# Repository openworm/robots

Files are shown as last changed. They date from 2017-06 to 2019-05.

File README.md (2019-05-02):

# robots
C. elegans robots.

The goal of this project is twofold:
1. To build a robot that simulates the neuromuscular function of a C. elegans nematode worm.
2. To specify a kit of parts and instructions that will allow a student to also build the robot.

The robot is controlled by a Raspberry Pi/ESP32 processor that contains a recorded simulation of the worm's
neuromuscular system (see references). The robot's body is a sequence of segments that mutually exert simulated muscle
contractions impemented by servos.

Folders:
1. WormHost: PC code to communicate with the onboard Raspberry Pi.
2. WormRPi: Raspberry Pi onboard code.
3. WormESP32: ESP32 onboard code.
4. WormSim: C. elegans neuromuscular simulator.
5. assembly: parts list, 3D printing .stl shape files, and assembly instructions.
6. docs: robot description.

References:
Boyle, Berri and Cohen, "Gait modulation in C. elegans: an integrated neuromechanical model", Front. Comput. Neurosci., 2012.
Eduardo J. Izquierdo and Randall D. Beer, "An Integrated Neuromechanical Model of Steering in C. elegans", ECAL15

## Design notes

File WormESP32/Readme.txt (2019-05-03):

C elegans worm robot with ESP32.
A distance sensor simulates food foraging by locating and moving toward the nearest object.

Power up the ESP32 and connect to its network: Robot_Worm
ESP32 IP address should be 192.169.4.1

Transfer python and segment_angles.txt to ESP32 using ftp.

FTP:
For linux:
In ftp connection, issue "passive" command to avoid attempt to open a server-to-client data connection.
This connection will be refused.
Cygwin:
Get ftp by installing inetutils package (also gets telnet).
FileZilla instructions:
https://github.com/loboris/MicroPython_ESP32_psRAM_LoBo/wiki/ftpserver

Login with telnet: 
telnet 192.168.4.1
login=micro, password=python

Run scripts:
1. To straighten robot:
exec(open("servo_reset.py").read())
2. To test servos:
exec(open("servo_test.py").read())
3. Run no food sensor:
exec(open("worm_run_segment_angles.py").read())
4. Run with laser distance food sensor:
exec(open("worm_run_segment_angles_laser.py").read())
5. Run with ultrasonic distance food sensor:
exec(open("worm_run_segment_angles_sonic.py").read())

The maximim number of steps can be limited by creating a file named "max_steps.txt" containing the value.

Note: power cycle board if you encounter python errors after repeated runs.

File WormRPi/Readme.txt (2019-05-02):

C elegans worm robot Raspberry Pi Zero W code.

Download Raspbian to SD boot card.

To enable wireless, create wpa_supplicant.conf in boot directory with this content:
country=<country code, e.g. US>
ctrl_interface=DIR=/var/run/wpa_supplicant GROUP=netdev
update_config=1

network={
    ssid="<network name>"
    psk="<network password>"
}

To enable ssh, create file named "ssh" in boot directory.

To find RPi IP: nmap -sn 192.168.1.0/24

Enable I2C:
https://www.abelectronics.co.uk/kb/article/1/i2c--smbus-and-raspbian-linux

Login with ssh:
ssh <RPi IP>
login=pi, password=raspberry

Setup:
1. Create $HOME/robot directory on RPi:
mkdir $HOME/robot
2. Copy python and segment_angles.txt files to $HOME/robot.

Run scripts: servo_reset.py (straighten robot), worm_run.py, worm_run_angles.py, worm_run_segment_angles.py

Ultrasonic distance sensor:

Parallax Ping Ultrasonic distance sensor:
https://www.parallax.com/sites/default/files/downloads/28015-PING-Sensor-Product-Guide-v2.0.pdf
See: sonar.py

Deprecated audio sensor:
 
Audio microphone installation instructions:
https://learn.adafruit.com/adafruit-i2s-mems-microphone-breakout/
https://pinout.xyz/pinout/i2c#
See: food_listener.py

To set audio volume sensitivity:
Copy asoundrc.txt to $HOME/.asoundrc on the robot.
Run arecord first to "prime the pump"
Then either:
  alsamixer
    F6 to select snd_rpi_simple_card
    F4 to set volume
or
  amixer -M set Capture 50%
Finally to make sensitivity persistent:
  sudo alsactl store 1

To enable http communications with host:
1. Copy json files to $HOME/robot.
2. Start flask web server: python flask_app.py

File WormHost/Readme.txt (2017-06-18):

C elegans worm robot host code.

Standalone simulation: python worm_run.py 

Interface with RPi:
1. Set up RPi (see WormRPi)
2. Run get_sensors.py to get sensor values from robot.
3. Run put_muscles.py to send muscle activations to robot.

Run simulator with RPi: jupyter notebook, then open Celegans_robot.ipynb

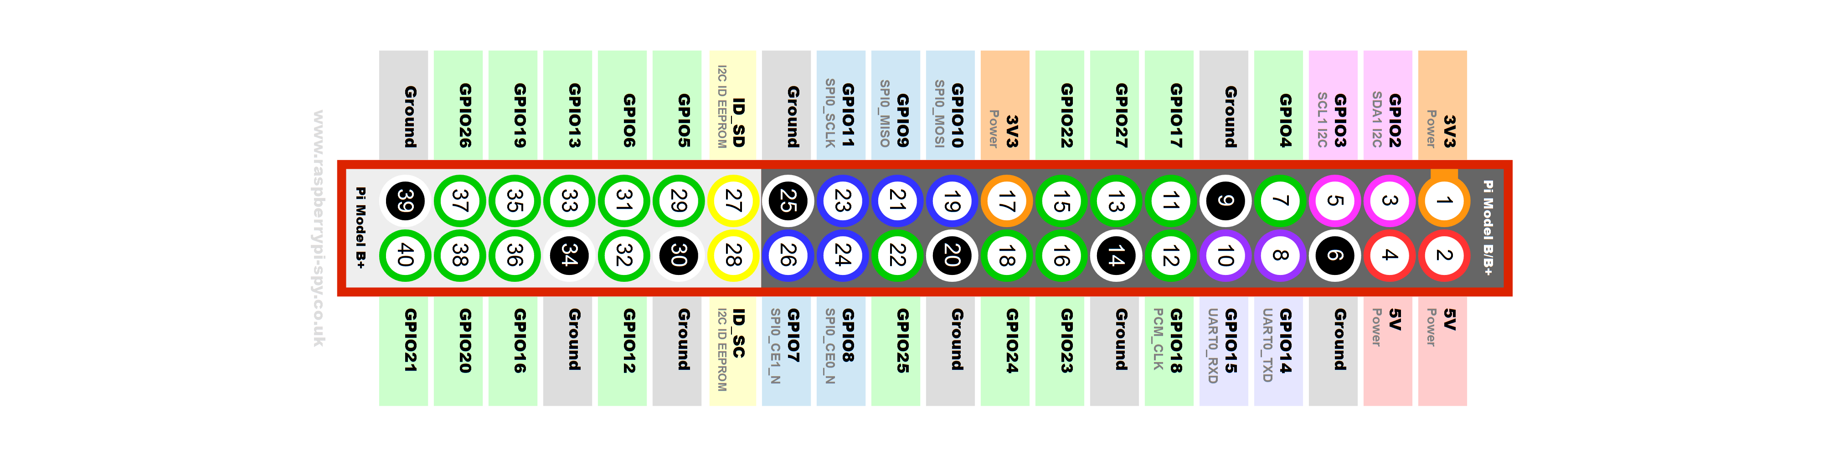
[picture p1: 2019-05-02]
WormRPi/Raspberry-Pi-GPIO-Layout-Model-B-Plus-rotated.png

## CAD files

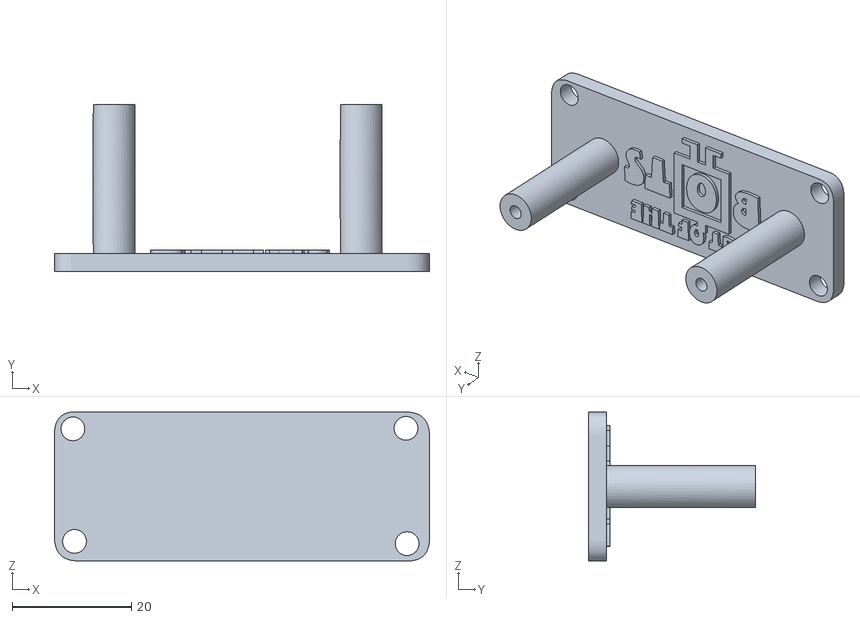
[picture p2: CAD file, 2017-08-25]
assembly/Worm_RPi_PWM_Stand.stl
63.0 x 28.0 x 25.0

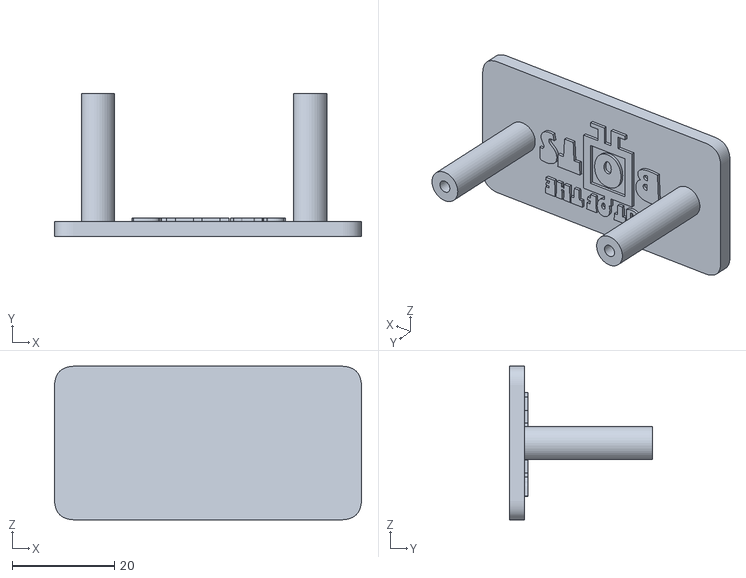
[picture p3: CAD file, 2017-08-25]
assembly/Worm_battery_stand.stl
60.0 x 28.0 x 30.0

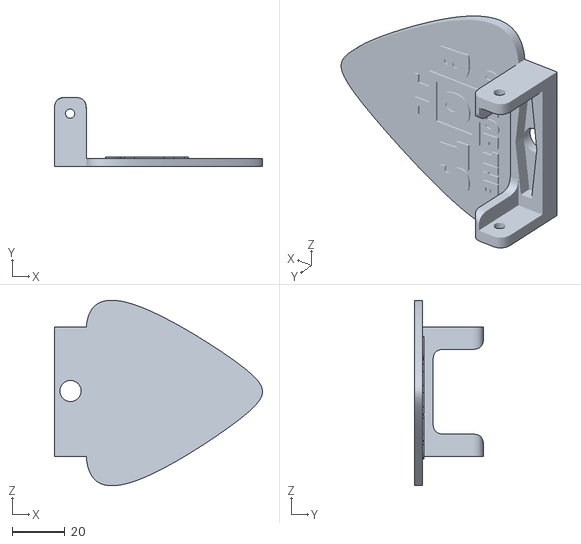
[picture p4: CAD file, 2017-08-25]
assembly/Worm_Head.stl
78.5 x 26.0 x 70.0

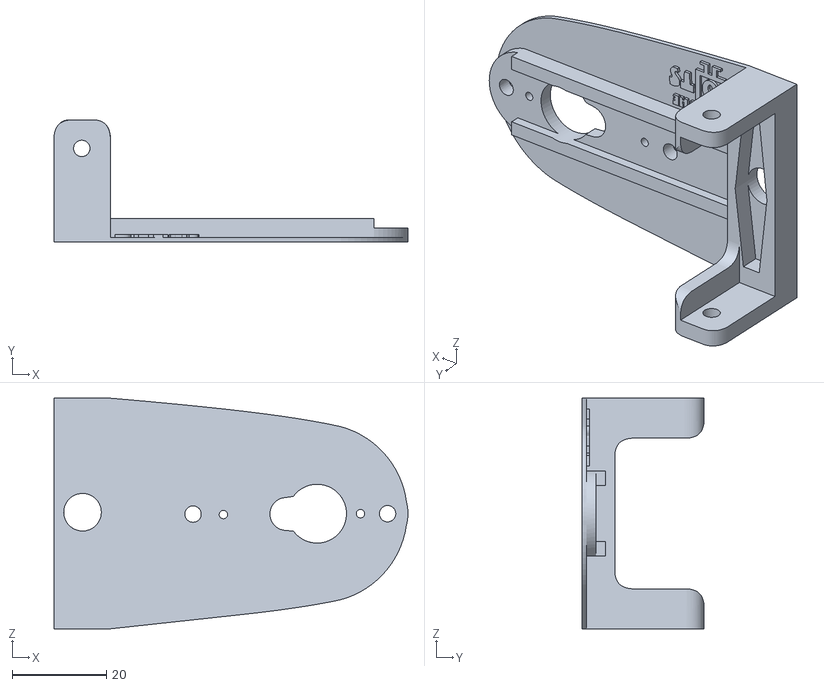
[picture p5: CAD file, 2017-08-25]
assembly/Worm_Body.stl
75.2 x 26.0 x 49.0

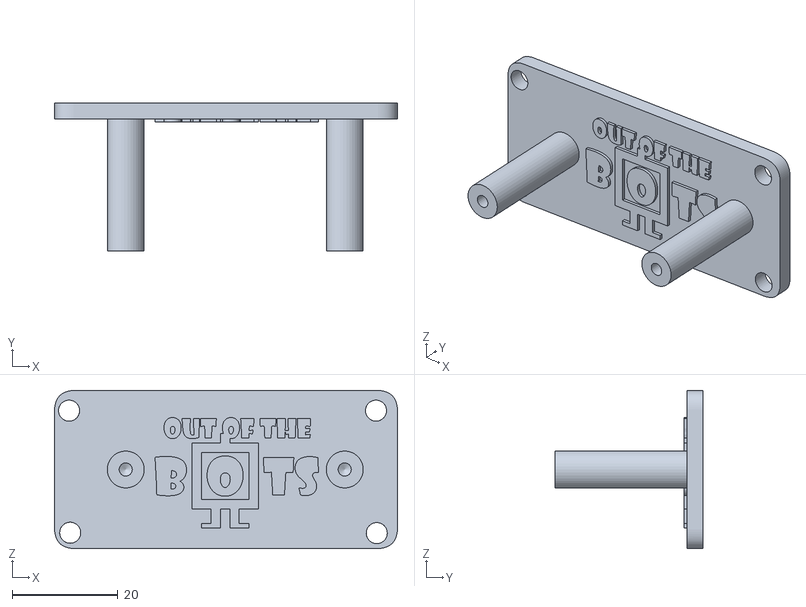
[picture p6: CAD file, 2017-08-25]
assembly/Worm_Stand.stl
65.0 x 28.0 x 30.0

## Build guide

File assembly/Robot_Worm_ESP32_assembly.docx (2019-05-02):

Robot Worm ESP32 Parts List

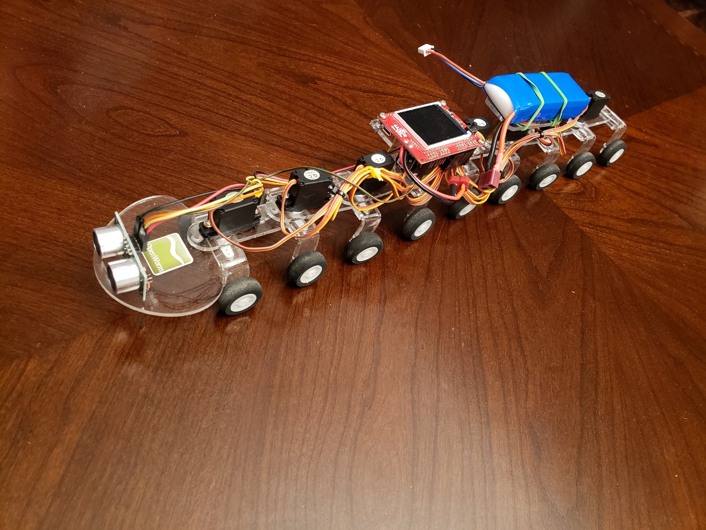
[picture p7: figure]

Demo videos: https://www.youtube.com/watch?v=BD-n1SASU4I, https://www.youtube.com/watch?v=OIZyOVygVxw, https://www.youtube.com/watch?v=ta4kQ2Gs8iM

Use the Raspberry Pi assembly video for assembly of segments, wheels, and servos: https://www.youtube.com/watch?v=6gbrbjGFhD4&feature=youtu.be

ESP32 board:

Order from Out of the BOTS: https://www.facebook.com/outofthebots/

Laser-cut body parts also available in lieu of 3D printing them.

3D printed body segments: see .stl files.

Wheels : This part isn’t critical and easily exchanged for what is easily available locally. I used 25mm RC aircraft wheels then drilled out the axle holes to 3mm purchased from here from here https://www.aliexpress.com/item/100pcs-Small-Light-Foam-Tail-Wheel-Diam-25mm-Thickness-11mm-Shaft-hole-2mm-For-RC-Remote/32705923540.html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,searchweb201602_4_10152_10065_10151_10130_10068_5010017_10136_10157_10137_10060_10138_10131_10155_10062_10132_10156_10133_437_10154_10056_10055_10054_10059_303_100031_10099_10103_10102_10096_10147_10052_10053_10050_10107_10142_10051_5020019_10084_10083_10080_10082_10081_10110_519_10175_10111_10112_10113_10114_10037_10182_10185_10032_10078_10079_10077_10073_10123_142,searchweb201603_13,ppcSwitch_4&btsid=c1dbe6fc-0b51-4f03-8d57-6b99288429d4&algo_expid=840bed72-95b2-42cf-bef2-a14471322b64-1&algo_pvid=840bed72-95b2-42cf-bef2-a14471322b64

Battery: 7.4V 2S 2000mAh 25C LiPolymer Battery T plug

https://www.ebay.com/i/263959891231?chn=ps

https://www.ebay.com/p/7-4-V-Battery-Charger-for-Double-Horse-RC-Helicopter-DH-9050-9053-9097-9100-9101/1948211389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

Servos: Corona brand model CS-939MG I brought directly from factory here: https://wxrgdz.en.alibaba.com/product/60608230195-804446832/Corona_CS939MG_Analog_Metal_Gear_Servo_2_5kg_0_14sec_12_5g_for_RC_toys.html

Also: https://hobbyking.com/en_us/corona-939mg-metal-gear-servo-2-5kg-0-14sec-12-5g.html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

You will also need some jumper wires and soldering iron.

F-F jumper wires: https://www.adafruit.com/product/1949

Optional low battery alarm:

http://www.ebay.com.au/itm/LED-RC-Lipo-Li-ion-Battery-Low-Voltage-Meters-Alarms-Test-Buzzer-Monitor-KB/232225019917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

Also: https://www.amazon.com/dp/B00SCJOITA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 (https://www.amazon.com/dp/B00SCJOITA?creative=395033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)

Food distance sensors:

1. Laser distance sensor VL53L0X:

https://www.aliexpress.com/item/GY-530-VL53L0X-Laser-Ranging-Sensor-Time-of-Flight-ToF-Distance-Measurement-Module-2-8-5V/32858618341.html

https://learn.adafruit.com/adafruit-vl53l0x-micro-lidar-distance-sensor-breakout

repository: https://bitbucket.org/thesheep/micropython-vl53l0x/src/9077f84e25409532b7ef220fa068605c971ba967/vl53l0x.py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

code: vl53l0x.py and worm_run_segment_angles_laser.py

pin connections: vin -> 3v3, gnd -> gnd, sda -> 32, scl -> 33

2. US-100 Ultrasonic Distance Sensor (HCSR04 low voltage clone):

https://www.bananarobotics.com/shop/US-100-Ultrasonic-Distance-Sensor-Module

code: hcsr04.py and worm_run_segment_angles_sonic.py

pins: servo 0-7 -> pins 7-0

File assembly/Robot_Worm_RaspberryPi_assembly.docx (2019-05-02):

Robot Worm RPi Parts List

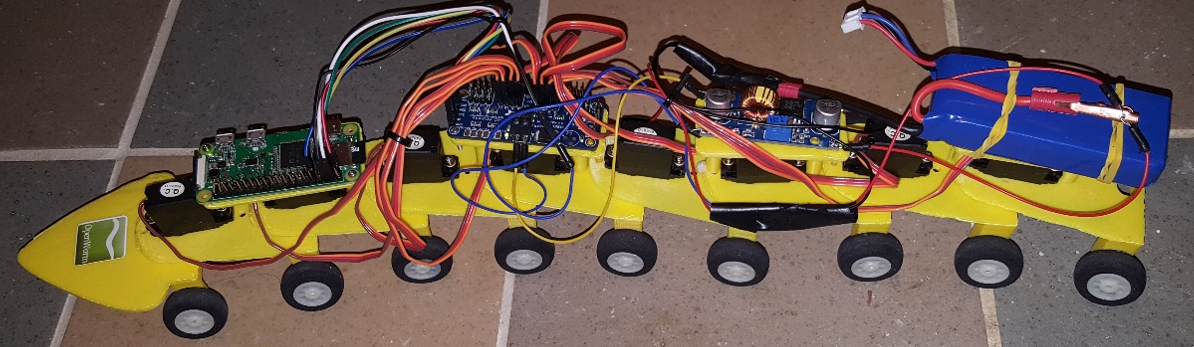
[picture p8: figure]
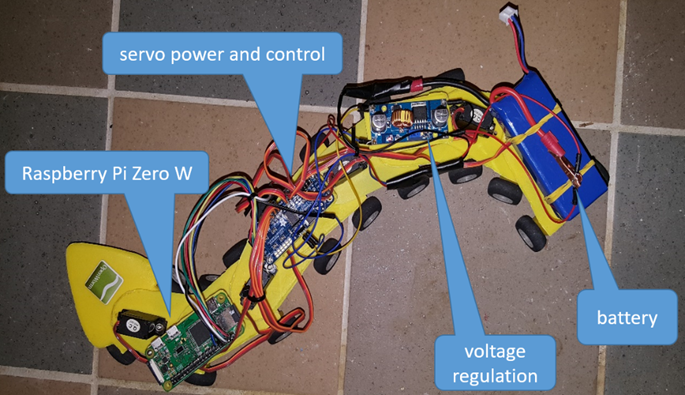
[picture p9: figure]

Demo video: https://www.youtube.com/watch?v=z1zARL2_4oM

Raspberry Pi assembly video: https://www.youtube.com/watch?v=6gbrbjGFhD4&feature=youtu.be

Video topics:

Time:

0:0

Discussion of body parts; attaching wheels.

3:03

Attaching servos to segments.

4:58

Attaching boards, e.g. Raspberry Pi, and other components to segments.

8:16

Connecting power and adjusting voltages.

13:15

Connecting boards using RPi pinout diagram.

17:12

Logging on the the RPi; calibrating the servos; connecting segments.

19:10

Ordering segments with various component platforms.

22:03

Finishing discussion.

3D printed body segments: see .stl files.

Wheels : This part isn’t critical and easily exchanged for what is easily available locally. I used 25mm RC aircraft wheels then drilled out the axle holes to 3mm purchased from here from here https://www.aliexpress.com/item/100pcs-Small-Light-Foam-Tail-Wheel-Diam-25mm-Thickness-11mm-Shaft-hole-2mm-For-RC-Remote/32705923540.html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,searchweb201602_4_10152_10065_10151_10130_10068_5010017_10136_10157_10137_10060_10138_10131_10155_10062_10132_10156_10133_437_10154_10056_10055_10054_10059_303_100031_10099_10103_10102_10096_10147_10052_10053_10050_10107_10142_10051_5020019_10084_10083_10080_10082_10081_10110_519_10175_10111_10112_10113_10114_10037_10182_10185_10032_10078_10079_10077_10073_10123_142,searchweb201603_13,ppcSwitch_4&btsid=c1dbe6fc-0b51-4f03-8d57-6b99288429d4&algo_expid=840bed72-95b2-42cf-bef2-a14471322b64-1&algo_pvid=840bed72-95b2-42cf-bef2-a14471322b64

Nuts and bolts: I used 3mm x 20mm bolts with nyloc nuts. It is critical that nyloc nuts r used

PMW board: This drives all the servos this is one from Adafruit https://www.adafruit.com/product/815 but I used this 1 with same chip so same software to drive it but this 1 is better built and cheaper http://www.ebay.com.au/itm/PCA9685-16-Channel-12-bit-PWM-Servo-motor-Driver-I2C-Module-For-Arduino-Robot-P6/182391317074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

Battery: I used a RC 7.4v 2S battery (you will need a discharge rate of min 3c but most RC batteries are like 25c so generally lots more than needed) the capacity doesn’t matter so much but I used 2000mah as it seemed to be a nice balance between size and lasting long enough before going flat. This is 1 I picked out for you guys just because it comes with a charger http://www.ebay.com.au/itm/1x-2x-2000mAh-7-4V-25C-LiPo-Battery-2S-Balance-Charger-for-Syma-X8HG-Drone-/332136206449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

Also: http://www.ebay.com/itm/like/191931347026?chn=ps&dispItem=1

Voltage step down converters: I had to use 2 of them I used the an adjustable micro 360 for the RPi and adjusted it to 5v see http://www.ebay.com.au/itm/5pcs-Mini-360-DC-DC-Buck-Converter-Step-Down-Module-4-75V-23V-to-1V-17V-/122098217064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

Also: http://www.ebay.com/itm/like/351738012331?chn=ps&dispItem=1

For the servos I used a larger amp adjustable conveter and adjusted it to 6v something like this http://www.ebay.com.au/itm/XL4015-5A-DC-DC-Step-Down-Buck-Converter-Module-Power-Supply-LED-Lithium-Charger/192234308138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

Also: http://www.ebay.com/itm/like/112237134540?chn=ps&dispItem=1

Servos: I used Corona brand model CS-939MG I brought directly from factory here https://wxrgdz.en.alibaba.com/product/60608230195-804446832/Corona_CS939MG_Analog_Metal_Gear_Servo_2_5kg_0_14sec_12_5g_for_RC_toys.html

Also: https://hobbyking.com/en_us/corona-939mg-metal-gear-servo-2-5kg-0-14sec-12-5g.html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

Optional low battery alarm:

http://www.ebay.com.au/itm/LED-RC-Lipo-Li-ion-Battery-Low-Voltage-Meters-Alarms-Test-Buzzer-Monitor-KB/232225019917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

Also: https://www.amazon.com/dp/B00SCJOITA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 (https://www.amazon.com/dp/B00SCJOITA?creative=395033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)

You will also need some jumper wires from and some 3amp power wires and soldering iron and multimeter for adjusting the voltage on buck converters.

F-F jumper wires: https://www.adafruit.com/product/1949

Optional food distance sensors:

1. Microphone.

https://www.adafruit.com/product/3421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

see: food_listener.py

2. Parallax PING))) ultrasonic distance sensor.

https://www.parallax.com/sites/default/files/downloads/28015-PING-Sensor-Product-Guide-v2.0.pdf

driver: sonar.py

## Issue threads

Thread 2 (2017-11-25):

1.1: Backwards motion

mstachowsky, 2017-11-25:
The robot/simulator should be able to move backwards as well as forwards.  We should be able to easily switch between backward/forward motion.  Backward and forward motion should be not able to occur at the same time.

mstachowsky, 2017-11-25:
I've found a paper that extends the current simulation we are using here: https://arxiv.org/abs/1707.05359  I've started integrating their code into ours just for testing purposes.  I have successfully gotten the simulator to move the worm backwards.  Next steps are to integrate this code in an intelligent and well-organized way, since right now it's a major hack

mstachowsky, 2017-12-02:
This is nearing completion.  The inhibition of motion (backward and forward cannot be initiated at the same time) remains.  However, that's a problem for the command neurons, not the motor programs.

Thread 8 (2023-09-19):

wormpy.py in WormHost doesn't have get_segment_angles method!

LucianSheen, 2023-09-19:
I tried to add:
def get_segment_angles(segment):
    return _wormpy.get_segment_angles(segment)
get_segment_angles = _wormpy.get_segment_angles

but it seems _wormpy.pyd doesn't have get_segment_angles either.

portegys, 2023-09-19:
Looks like that function is missing. If you want to read the segment angles
though they are in a file called "segment_angles.txt" and code in
worm_run_segment_angles.py reads the file and moves the robot.

On Tue, Sep 19, 2023 at 2:39 PM LucianSheen ***@***.***>
wrote:

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

LucianSheen, 2023-09-19:
Thanks for the reply, portegys!
But also I am wondering then how come the segment angle text file was generated,
had a look at the worm_gen_segment_angles.py and it basically has got missing functions as well(also incl.get_segment_angles).
As I can not decode the _wormpy.pyd file, it made me wonder if the project itself is more about worms' locomotion,
rather than recreating c.elegans' connectome in robotics?

Best,
Lucian

portegys, 2023-09-19:
Hi Lucian,
We actually got the angles from running the code associated with this
project:
Boyle, Berri and Cohen, "Gait modulation in C. elegans: an integrated
neuromechanical model", Front. Comput. Neurosci., 2012.
Which is a physics simulation of the worm.
Tom

On Tue, Sep 19, 2023 at 4:33 PM LucianSheen ***@***.***>
wrote:

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

LucianSheen, 2023-09-19:
Hello Tom! yes I have read the document just now and realised it is based on their research, sorry for that.
I wanted to get this code work with a flexibility of different number of servos like 12 or 16,
as per apparently the code was originally designed to be like?

Best,
Lucian

portegys, 2023-09-19:
Oh right. The worm actually has 12 segments, but we cut it down to 8 or so
for the robot.

On Tue, Sep 19, 2023 at 4:51 PM LucianSheen ***@***.***>
wrote:

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

LucianSheen, 2023-09-25:
Thanks!
could you please kindly let me know what I should do if I want to run and
make my own simulation model and create angle text file based on the
simulation?

Many Thanks,
Lucian

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

portegys, 2023-09-25:
Here is a link with the code to run the simulation and generate both the
segment angles (all 12 of them) and the muscle activations. There are also
makefiles, visual studio files, and python scripts to run it.
https://www.dropbox.com/scl/fi/5y9ojiby948nrsxr89py7/WormSim.zip?rlkey=gpvsx1dlug6z06cyb2p6flimw&dl=0
Tom

On Mon, Sep 25, 2023 at 6:45 AM LucianSheen ***@***.***>
wrote:

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

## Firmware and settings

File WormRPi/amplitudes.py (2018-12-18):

"""Usage:
    amplitudes WAV_FILE

    Returns the (linear) amplitude of the signal inside the wav file, sample by sample.
"""
from __future__ import division
import docopt

import scipy.io.wavfile

MAX_WAV16_AMP = 32767  # = 2**15-1  # because wav16 is signed (wav8 isn't)


def main():
    args = docopt.docopt(__doc__)

    one_pos_to_neg_crossing_path = r"W:\materials\audio\one_pos_to_neg_crossing.wav"
    if False: args['WAV_FILE'] = one_pos_to_neg_crossing_path

    rate, amp_arr = scipy.io.wavfile.read(args['WAV_FILE'])
    for amp in (amp_arr / MAX_WAV16_AMP):
        print(amp)

if __name__ == '__main__':
    main()

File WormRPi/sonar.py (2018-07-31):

# Sonar distance to nearby object.
# Using Parallax PING))) ultrasonic distance sensor.
# https://www.parallax.com/sites/default/files/downloads/28015-PING-Sensor-Product-Guide-v2.0.pdf

import time
import RPi.GPIO as GPIO

GPIO.setmode(GPIO.BOARD)

timeout = 0.020

def ping():

        GPIO.setup(11, GPIO.OUT)
        #cleanup output
        GPIO.output(11, 0)

        time.sleep(0.000002)

        #send signal
        GPIO.output(11, 1)

        time.sleep(0.000005)

        GPIO.output(11, 0)

        GPIO.setup(11, GPIO.IN)
        
        goodread=True
        watchtime=time.time()
        while GPIO.input(11)==0 and goodread:
                starttime=time.time()
                if (starttime-watchtime > timeout):
                        goodread=False

        if goodread:
                watchtime=time.time()
                while GPIO.input(11)==1 and goodread:
                        endtime=time.time()
                        if (endtime-watchtime > timeout):
                                goodread=False
        
        if goodread:
                duration=endtime-starttime
                distance=duration*34000/2
                return distance
        else:
                return -1.0

if __name__ == '__main__':
    print ping()

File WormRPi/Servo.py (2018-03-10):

# Copyright (c) 2017 Out of the BOTS
# http://outofthebots.com.au/
# Author: Shane Gingell
#
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


# Servo class provides very basic functionality for controlling 
# sevoing using the PCA9685 chipset with a RPi. 


import smbus #import the System Mangement package for I2C coms
import time

class Servo :

  global bus
  global address
  bus = smbus.SMBus(1) #RPi3 uses bus 1 but if using bus 0 then change here
  address = 0x40 #factory standard I2C slave address change if needed
  
  @classmethod
  def __init__(self): #initizing will turn on all servos and set to poiition 0
    bus.write_byte_data(address, 0x01, 0x04)
    bus.write_byte_data(address, 0x00, 0x01)
    time.sleep(0.005)

    oldreg0 = bus.read_byte_data(address, 0x00)
    newreg0 = (oldreg0 & 0x7F) | 0x10
    bus.write_byte_data(address, 0, newreg0)

    prescale = int((25000000/(4096*50))-1)
    bus.write_byte_data(address, 0xFE, prescale)

    bus.write_byte_data(address, 0, oldreg0)
    time.sleep(0.005)
    bus.write_byte_data(address, 0, oldreg0 | 0x80)

    bus.write_byte_data(address, 0xFA, 0)
    bus.write_byte_data(address, 0xFB, 0)
    bus.write_byte_data(address, 0xFC, 0x33)
    bus.write_byte_data(address, 0xFD, 0x01)  
  
  def set_servo (self,servo_number, position): #routine for setting servo positions. no error checking
	step = 202/90
	if position < -90 : position = -90
	if position > 90 : position = 90
	if position == 0 : offtime = 307	
	else  : offtime = 307 + (step * position)    
	startreg = servo_number * 4 + 8    
	bus.write_byte_data(address, startreg, offtime & 0xff)    
	bus.write_byte_data(address, startreg+1, offtime >> 8)

#still much funtionality missing especally a shutdown down function.
  

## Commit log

2017-06-18 Initial host and Raspberry Pi code
2017-06-19 Fix duplicate file close
    [wormsim.cpp]
2017-08-25 Shapefiles and docs
    [Worm Body 11-8-17.stl, Worm_Head.stl, Worm_PWM_Stand.stl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]
2017-11-05 Control servos with segment angles
2017-11-21 Update README.md
    [] edited step 5 to include additional build options you may need if your system's make isn't configured correctly
    [] edited step 7 to indicate Octave will work
    [] Added step 10 to explain how to export the frames of the simulation using the export_fig package
2018-03-10 Add parts list
    [Worm Body 11-8-17.stl, Worm_Head.stl, Worm_PWM_Stand.stl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]
2018-07-31 Add sonar.py for disance sensor
2018-12-18 ESP32 processor replacement for Raspberry Pi
    [amplitudes.py, worm_run.py, worm_run_angles.py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]
2019-05-02 ESP32 food foraging with ultrasonic distance sensor
    [Worm_Body.stl, Worm_Head.stl, Worm_RPi_PWM_Stand.stl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]
